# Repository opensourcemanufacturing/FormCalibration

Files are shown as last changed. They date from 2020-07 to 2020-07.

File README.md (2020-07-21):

# FormCalibration
Calibration Tests For the Formlabs Form1+

# Galvo Alignment Verification

# Never look look inside the Form 1+ when the laser is on. Never run the laser with the orange cover open. Wear appropriate PPE (personal protective equipment). Protect your eyes. Proceed at your own risk!

At this time, the following procedure requires a Windows PC because the tools I've created are Windows Executables.

1) Remove the rear panel of your Form 1+
2) Connect your Form 1+ to your PC via USB.
3) Download and install the OpenFL version of Preform on your Windows PC: https://s3.amazonaws.com/FormlabsReleases/Release/2.3.3/PreForm_setup_2.3.3_release_OpenFL_build_2.exe
4) Download and run Zadig: https://github.com/pbatard/libwdi/releases/download/b730/zadig-2.5.exe
  A) Select the Options Menu at the top of the window, and ensure that "List All Devices" has a check mark next to it.
  B) Select the drop down in the upper center of the window, and select "Form1" from the list.
  C) In the center of the screen to the right of the green arrow there is a selection box, click the down arrow button next to the selection box until the "libusbK (v3.0.7.0)" option is selected.
  D) Click the Replace Driver button and wait for the "The Driver was Installed Successfully" message.
  E) Close Zadig (you can delete it from your PC now if you want to).
5) Install a clean/empty vat and a clean build plate in the Form 1+
6) Cut a piece of white paper and trim so that fits inside the vat, covering the entire print area. It needs to be larger than the build plate and lay flat in the bottom of the vat.
7) Download the OpenFL executables: https://github.com/opensourcemanufacturing/OpenFL/releases/download/0.01/OpenFL_Executables.zip
8) Unzip OpenFL Executables and run "Z_Jog_052320.exe" (please wait - it may take a moment for the application to start, this is normal)
  A) Select the "5 milimeter" radio buttom
  B) Click the "Z Down" button until the build plate is close to the vat. You can then use the 1mm setting to move the build plate closer to the paper, you only need it to be close enough that you can trace the shape of the build plate onto the paper.
  C) Trace the outline of the build plate onto the paper.
  D) Press the "Home All" button.
  E) Once the homing sequence finishes, Press the "Exit" button.
  F) Without removing the paper and without shifting it's position in the vat, carefully measure and draw a line across the center of the build plate outline from side to side and another line from front to back. You can use a strip of paper to find the center point (see the pictures below).
  G) Leave the paper in the vat for the rest of the process.
  H) Remove the build platform for the rest of the process.
9) Download and unzip the galvo calibration files: https://github.com/opensourcemanufacturing/FormCalibration/releases/download/0.01/Galvo.Calibration.Files.zip
10) Run the Preform software you installed in Step 3 (if it is currently running, it is a good idea restart it)
  A) Open the Printers Window (select File > Printers), expand your printer and run the firmware update.
  B) Open the "Fine Tuning" window and make sure your X/Y Offsets are both set to 0.00mm.
  B) Open the Printer Settings (lower right corner of Preform). Ensure that the Form 1+ option is selected, then click "Load Custom Material..." and select the "GalvoCalibration.ini" file from the Galvo Calibration files you downloaded in Step 8.
  C) Make sure the cover is closed on your Form 1+, then open and print the "GalvoCalibrationModel.form" file you unzipped in step 8.
  D) Observe the pattern of the cross that is drawn by the galvonometers. It should cross the center of the build plate outline you drew in Step 7; if the alignment is off, continue below.
  
# Never look look inside the Form 1+ when the laser is on. Never run the laser with the orange cover open. Wear appropriate PPE (personal protective equipment). Protect your eyes. This involves putting your hands inside of a piece of equipment that is energized with electricity. Proceed at your own risk!

# Galvo adjustment - Keep the cover closed!

1) While the printer is turned off (or paused - be smart about this), loosen the cap screw the galvo you intend to adjust. Position the printer so you cannot see inside the rear cover, and carefully hold the body of the galvo with one hand.
2) With your other hand press the button to unpause the print job. As the pattern is printed, slowly and carefully rotate the body of the galvo until the axis is aligned with the lines you drew in the vat.
3) When you are satisfied with the alignment of that axis, turn off the printer (or pause it - be smart about this) and tighten the cap screw for that galvo. 
4) Repeat steps 1-3 for the other axis, if necessary.
5) Congratulations, you've manually adjusted your galvos!

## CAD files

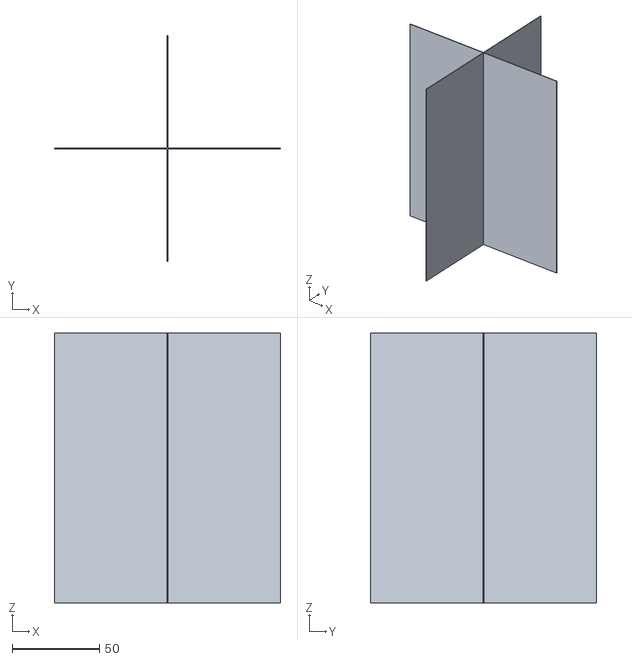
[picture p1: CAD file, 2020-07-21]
Form 1+ Galvo Calibration.stl
130.0 x 130.0 x 155.0

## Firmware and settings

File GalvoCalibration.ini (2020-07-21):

;;;;;;;;;;;;;;;;; FORMLABS MATERIAL CONFIGURATION ;;;;;;;;;;;;;;;;;
;;;;;;;;;;;;;;;;;;;;;;;;;;;;;;;;;;;;;;;;;;;;;;;;;;;;;;;;;;;;;;;;;;;
;;;;;;;;;;;;;;;;;;;;;;;;;;;;;;;;;;;;;;;;;;;;;;;;;;;;;;;;;;;;;;;;;;;
;;;;;;;;;;;;   ,;;;;;;;;;;;;;;;;;;;;;;;;;;;;;;;;;;;:   ;;;;;;;;;;;;
;;;;;;;;,    :     ;;;;;;;;;;;;;;;;;;;;;;;;;;;;;`         `;;;;;;;;
;;;;;;;   ;;;;;;;,    ;;;;;;;;;;;;;;;;;;;;;;;               ;;;;;;;
;;;;;;;         `;;;;    ,;;;;;;;;;;;;;;;:                  ;;;;;;;
;;;;;;;;.  ;;;;`       ,     ;;;;;;;;;`             ;;;;   ;;;;;;;;
;;;;;;;;;;   ;;;;;;;;;          ;;;          :;;;;;;;;:  :;;;;;;;;;
;;;;;;;;;;;;   ;;;;;;;;;;;;;;;.     ,;;;;;;;;;;;;;;;;  ,;;;;;;;;;;;
;;;;;;;;;;;;;   ;;;;;;;;;;;,     ,     ,;;;;;;;;;;;`  ;;;;;;;;;;;;;
;;;;;;;;;;;;;;,  :;;;;;;:        ;`       ,;;;;;;;   ;;;;;;;;;;;;;;
;;;;;;;;;;;;;;;;   ;;:    ;  `  ;;;          :;;;  .;;;;;;;;;;;;;;;
;;;;;;;;;;;;;;;;;      ;;   ;  :;;;;              ;;;;;;;;;;;;;;;;;
;;;;;;;;;;;;;;;;     :;;   ;   ;;;;;.              :;;;;;;;;;;;;;;;
;;;;;;;;;;;;;;   ;;;     ;;:  ;;;;;;;                ;;;;;;;;;;;;;;
;;;;;;;;;;;;;;,   ;;;: ,;;;  :;;;;;;;;              `;;;;;;;;;;;;;;
;;;;;;;;;;;;;;;;;   `;;;;;   ;;;;;;;;;,           ;;;;;;;;;;;;;;;;;
;;;;;;;;;;;;;;;;;;;`   ;;,  ;;;;;;;;;;;         ;;;;;;;;;;;;;;;;;;;
;;;;;;;;;;;;;;;;;;;;;;;    ;;;;;;;;;;;;;    ;;;;;;;;;;;;;;;;;;;;;;;
;;;;;;;;;;;;;;;;;;;;;;;;;;;;;;;;;;;;;;;;;;;;;;;;;;;;;;;;;;;;;;;;;;;
;;;;;;;;;;;;;;;;;;;;;;;;;;;;;;;;;;;;;;;;;;;;;;;;;;;;;;;;;;;;;;;;;;;
;;;;;;; WARNING: Modifying these settings can lead to damage ;;;;;;
;;;;;;;;;; to your Form 1+ and void its warranty. ;;;;;;;;;;;;;;;;;
;;;;;;;;;;;;;;;;;;;;;;;;;;;;;;;;;;;;;;;;;;;;;;;;;;;;;;;;;;;;;;;;;;;

;-----------------------------------------------------------------;
; Resin Calibration by X3msnake in 2019.02.20 with Moai FEP Vat
;-----------------------------------------------------------------;

[perimeter]
basexyfeedrate = 800  ; Laser speed in mm/s for the perimeter of the base (aka raft). (Faster than 800 mm/s may noticably reduce surface quality.)
baselaserpowermw = 17  ; Laser power in mW used for the perimeter of the base (aka raft). (max: 62 mW for Form 1+)
modelxyfeedrate = 800  ; Laser speed in mm/s for the perimeter of the model. (Faster than 800 mm/s may noticably reduce surface quality.)
modellaserpowermw = 16  ; Laser power in mW for the perimeter of the model (max: 62 mW for Form 1+)
supportxyfeedrate = 800  ; Laser speed in mm/s for the perimeter of the supports. (Faster than 800 mm/s may noticably reduce surface quality.)
supportlaserpowermw = 21  ; Laser power in mW for the perimeter of thesupports. (max: 62 mW for Form 1+)

[PrintSettings]
SliceHeight = 0.1  ; The layer thickness in mm. For example 0.1 is 100 microns. Be aware that values not corresponding to whole z-motor microsteps (0.0025 mm) will be rounded.
ScanlineSpacing = 0.09  ; Spacing of fill lines in mm.
InnerBoundaryOffset = 0.12
OuterBoundaryOffset = 0.03  ; Offset from model perimeter to outermost outline in mm. Conceptually this is the curing radius of the outermost outline.
Xcorrectionfactor = 1.008  ; Scale factor for the x axis to account for shrinkage.
Ycorrectionfactor = 1.008  ; Scale factor for the y axis to account for shrinkage.
ScanlineBoundaryOffset = 0.03  ; Offset in mm from the innermost outline to the boundary of the fill. If this is zero, the fill touches the innermost outline; if this is positive it does not; if this is negative, the fill overlaps at least the inner outline.
OffsetsNum = 3  ; Number of outlines to draw. min: 0; max: unlimited

[Overview]
MaterialName = Peopoly Nex Grey V1

[laserRoutine]
firstlayerpasses = 20  ; The number of laser passes to do for layer 0 to attach to the build platform.
otherlayerpasses = 20  ; The number of laser passes to do for most layers (typically 1).
earlylayerpasses = 20  ; The number of laser passes to do for early layers as defined by earlytimesexpose.
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
